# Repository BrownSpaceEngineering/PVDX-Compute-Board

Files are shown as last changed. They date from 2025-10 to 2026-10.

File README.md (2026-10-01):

# PVDX Compute Board

This repo contains kicad files for the PVDX Compute board, the main command/control interface for PVDX. The board contains: the SAMD51 microcontroller, 3 MRAM chips, an accelerometer, a 3-axis magnetometer, and headers for interfacing with the EPS, the battery board, the burn wire, the photodiodes, the ADCS/perovskite boards, the S-Band, the UHF, the display, and the ArduCam. 

The repo is organized into four main folders: 
1. Components (kicad symbols, footprints, and step files for each component not already built into the kicad libraries; shared between the other three folders)
2. SAMD51 Devboard (a simplified version for testing; it is run off USB-C, and houses only buck converters (not present on the final boards) and the SAMD51. All other components are exposed as headers. Every pin on the SAMD51 is also exposed)
3. Compute Board (the two layer implementation of the unified board containing all the final flight components with headers only for peripherals)
4. compute4layer (a copy of the Compute Board project with only the layout changed to a 4-layer (signal, GND, power, signal) stackup)

## Schematics 

Presented here are images of the schematics shared by the Compute Board and compute4layer: 




## Datasheets

For ease of access, here is a table of datasheets for the onboard components: 

| Component | Part number |
| --- | --- |
| SAMD51 | [Microchip ATSAMD51N19A](https://ww1.microchip.com/downloads/aemDocuments/documents/MCU32/ProductDocuments/DataSheets/SAM-D5x-E5x-Family-Data-Sheet-DS60001507.pdf) |
| MRAM | [Everspin EM008LX](https://datasheet.lcsc.com/datasheet/pdf/902c3bb2baf214246dee551af985b64a.pdf?productCode=C17289052) |
| Accelerometer | [Murata SCH16T-K01](https://sensorsandpower.angst-pfister.com/fileadmin/images/news/Datasheet-SCH16T-K01_JAN2024.pdf) |
| Magnetometer | [PNI RM3100](https://www.tri-m.com/products/pni/RM3100-User-Manual.pdf) |
| Buck converter | [Microchip MCP-1604-180I](https://ww1.microchip.com/downloads/aemDocuments/documents/OTH/ProductDocuments/DataSheets/22042B.pdf) |
| I2C Multiplexer | [TI TCA9546A](https://www.ti.com/lit/ds/symlink/tca9546a.pdf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) |

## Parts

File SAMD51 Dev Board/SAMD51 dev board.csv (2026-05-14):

Reference | Qty | Value | DNP | Exclude from BOM | Exclude from Board | Footprint | Datasheet | Manufacturer_Part_Number | Manufacturer_Name
C1,C2,C3,C4,C7,COUT1 | 6 | 4.7 uF |  |  |  | Capacitor_SMD:C_0402_1005Metric
C5,CIN1,CIN2,CIN3 | 4 | 10 uF |  |  |  | Capacitor_SMD:C_0402_1005Metric
C6 | 1 | 0.1 uF |  |  |  | Capacitor_SMD:C_0402_1005Metric
CIN4,CIN5,CIN6,COUT2 | 4 | 100 nF |  |  |  | Capacitor_SMD:C_0402_1005Metric
D1 | 1 | RED |  |  |  | LED_SMD:LED_0402_1005Metric
D2 | 1 | GREEN |  |  |  | LED_SMD:LED_0402_1005Metric
D3,D4 | 2 | ORANGE |  |  |  | LED_SMD:LED_0402_1005Metric
IC1 | 1 | MCP1603-330I_MC |  |  |  | MPC1603:MPC1603-330 | https://static6.arrow.com/aropdfconversion/4acbe9a1e3d4dc5e34c6ab3aecc61a4631ca5442/22042a.pdf | MCP1603-330I/MC | Microchip
IC2 | 1 | MCP1603-180I_MC |  |  |  | MPC1603:MPC1603-180 | https://static6.arrow.com/aropdfconversion/4acbe9a1e3d4dc5e34c6ab3aecc61a4631ca5442/22042a.pdf | MCP1603-330I/MC | Microchip
J1 | 1 | Conn_02x08_Top_Bottom |  |  |  | Connector_PinSocket_2.54mm:PinSocket_2x08_P2.54mm_Vertical
J2 | 1 | USB4105-GF-A |  |  |  | USBC:USB4105_GCT | USB4105-GF-A
J3 | 1 | FTSH-105-01-L-DV-007-K |  |  |  | JLink:SAMTEC_FTSH-105-01-L-DV-007-K
J4,J11 | 2 | Conn_01x07 |  |  |  | Connector_PinSocket_2.54mm:PinSocket_1x07_P2.54mm_Vertical
J5,J10,J14 | 3 | Conn_02x16_Top_Bottom |  |  |  | Connector_PinSocket_2.54mm:PinSocket_2x16_P2.54mm_Vertical
J6 | 1 | Conn_02x06_Top_Bottom |  |  |  | Connector_PinSocket_2.54mm:PinSocket_2x06_P2.54mm_Vertical
J7 | 1 | Conn_02x08_Counter_Clockwise |  |  |  | Connector_PinSocket_2.54mm:PinSocket_2x08_P2.54mm_Vertical
J8,J17 | 2 | Conn_01x10 |  |  |  | Connector_PinSocket_2.54mm:PinSocket_1x10_P2.54mm_Vertical
J9 | 1 | Conn_01x02 |  |  |  | Connector_PinSocket_2.54mm:PinSocket_1x02_P2.54mm_Vertical
J12 | 1 | Conn_01x05 |  |  |  | Connector_PinSocket_2.54mm:PinSocket_1x05_P2.54mm_Vertical
J13 | 1 | Conn_01x08 |  |  |  | Connector_PinSocket_2.54mm:PinSocket_1x08_P2.54mm_Vertical
J15,J16,J19 | 3 | Conn_01x06 |  |  |  | Connector_PinSocket_2.54mm:PinSocket_1x06_P2.54mm_Vertical
L1,L2 | 2 | 4.7uH |  |  |  | Inductor_SMD:L_0201_0603Metric
L3,L4 | 2 | 10 uH |  |  |  | Inductor_SMD:L_0402_1005Metric
R1,R2,R3,R4 | 4 | 1K |  |  |  | Resistor_SMD:R_0402_1005Metric
R5,R8 | 2 | 5.1k |  |  |  | Resistor_SMD:R_01005_0402Metric
R6,R7 | 2 | 22 |  |  |  | Resistor_SMD:R_01005_0402Metric
R9,R10 | 2 | 0 |  |  |  | Resistor_SMD:R_0402_1005Metric
R11,R12,R13,R14 | 4 | 10k |  |  |  | Resistor_SMD:R_0402_1005Metric
U1 | 1 | SAMD51 |  |  |  | SAMD51:TQFP128_14X14MC_MCH-L

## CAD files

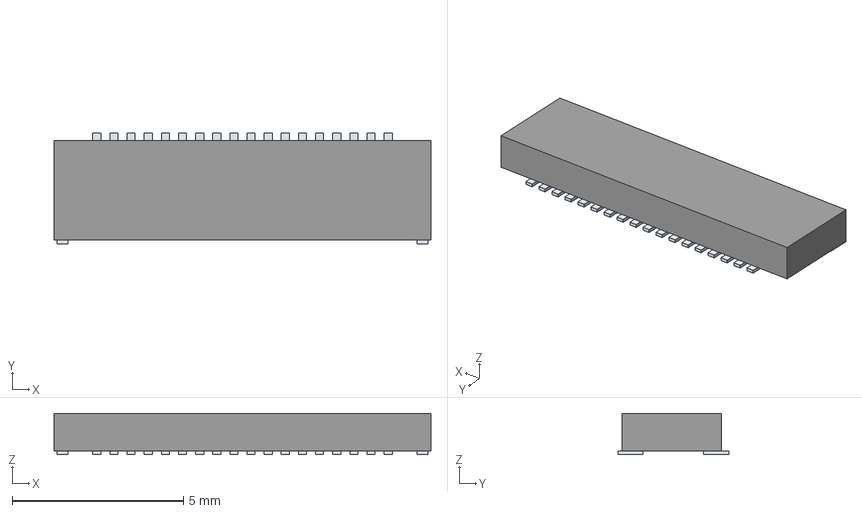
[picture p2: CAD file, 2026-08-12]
Components/18 Pin Ribbon Cable/FH34SRJ-18S-0.5SH_50_.stp
11.0 x 3.23 x 1.20 mm
Pins

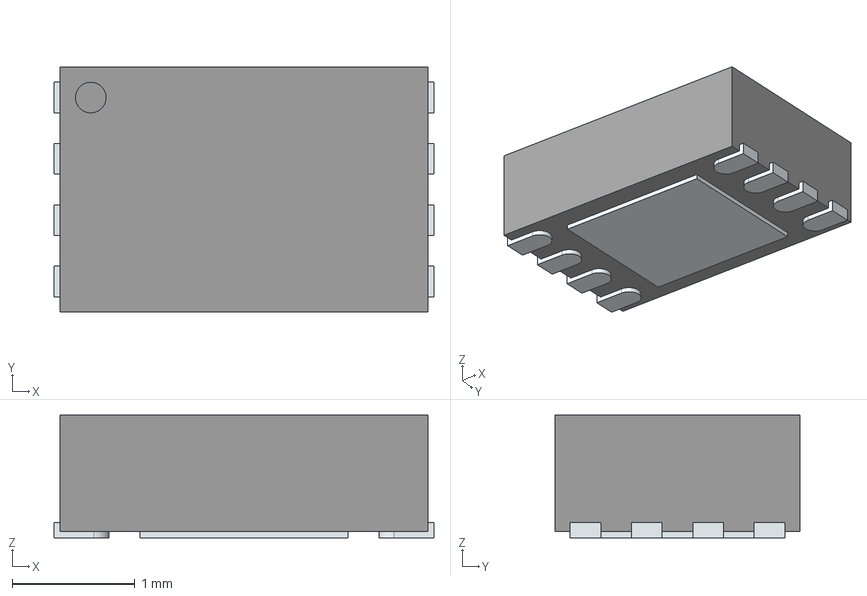
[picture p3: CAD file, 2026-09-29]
Components/Buck converters/MCP1603-330I_MC.stp
3.10 x 2.00 x 1.00 mm
ThermalPin
PinsArrayLR

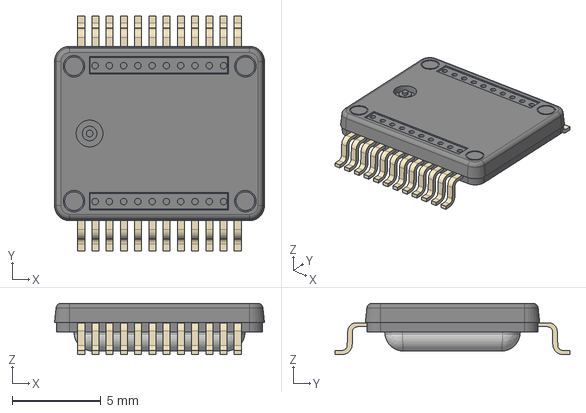
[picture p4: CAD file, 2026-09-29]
Components/Gyroscope/SCH16T-K01-1.stp
11.8 x 13.2 x 2.87 mm

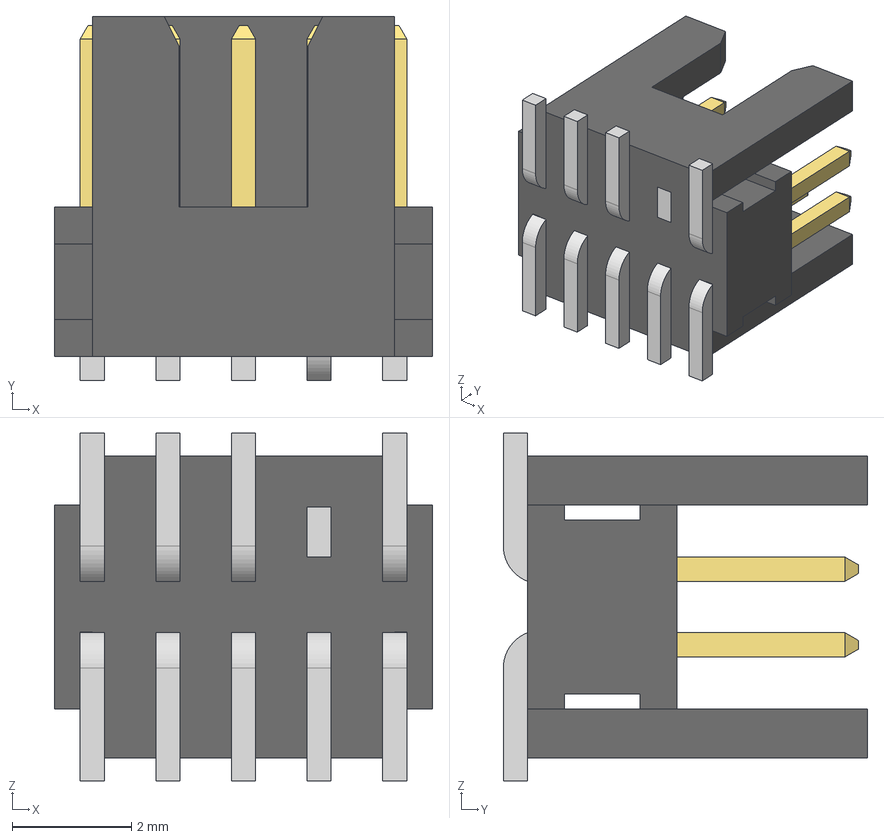
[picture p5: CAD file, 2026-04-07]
Components/J Link/FTSH-105-01-L-DV-007-K.step
6.35 x 6.12 x 5.84 mm
FTSH-105-01-L-DV-007-K_body
FTSH-105-01-L-DV-007-K_pins1
FTSH-105-01-L-DV-007-K_pins2

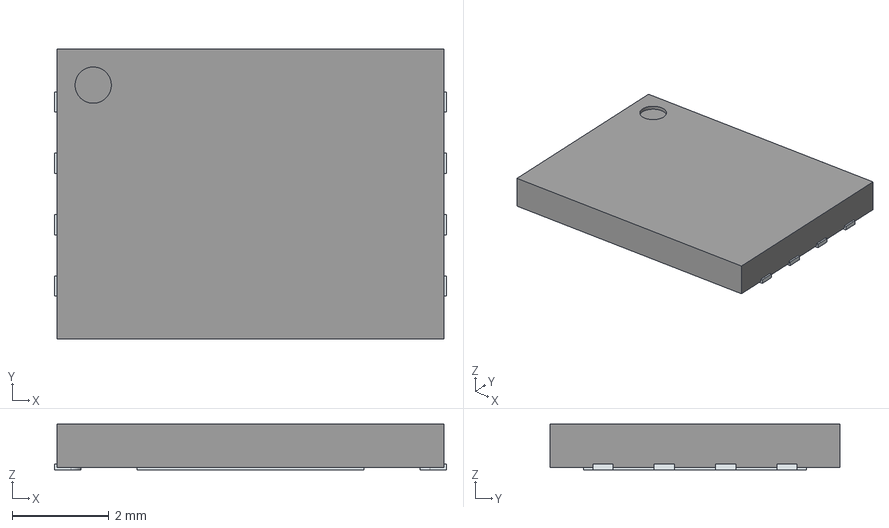
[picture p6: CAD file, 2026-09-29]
Components/MRAM/EM008LXQADG13IS1T.stp
8.10 x 6.00 x 0.95 mm
ThermalPin
PinsArrayLR

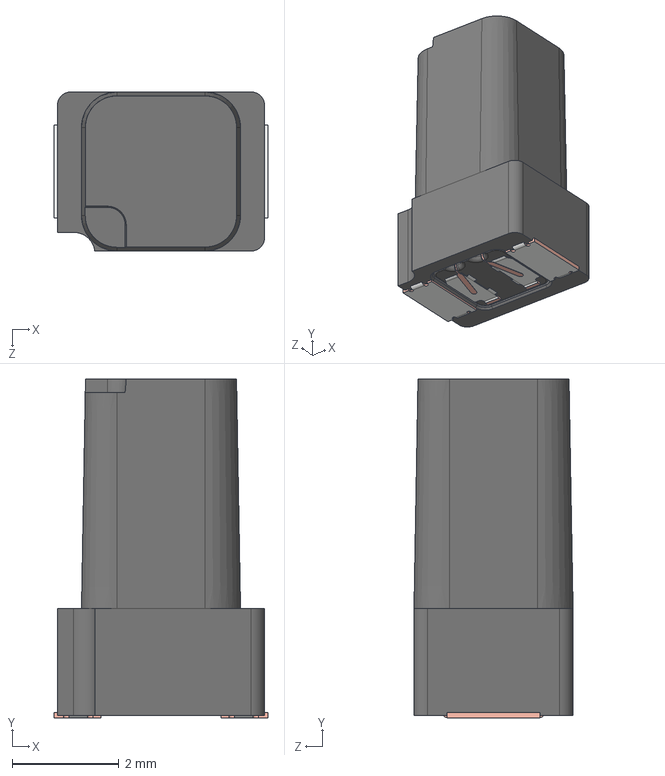
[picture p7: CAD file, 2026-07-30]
Components/RM3100/Sensor Sen-Z-f.STEP
4.00 x 6.35 x 2.98 mm

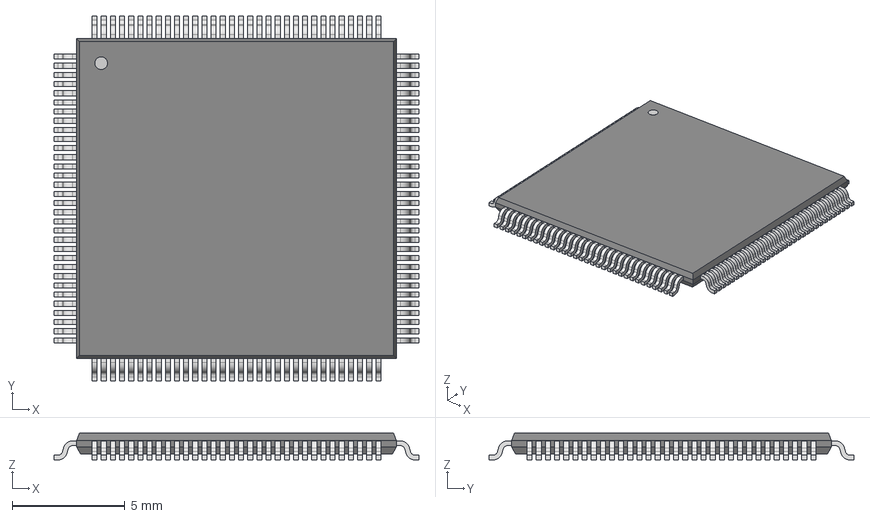
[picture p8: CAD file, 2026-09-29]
Components/SAMD51/TQFP128_14X14MC_MCH.step
16.2 x 16.2 x 1.20 mm

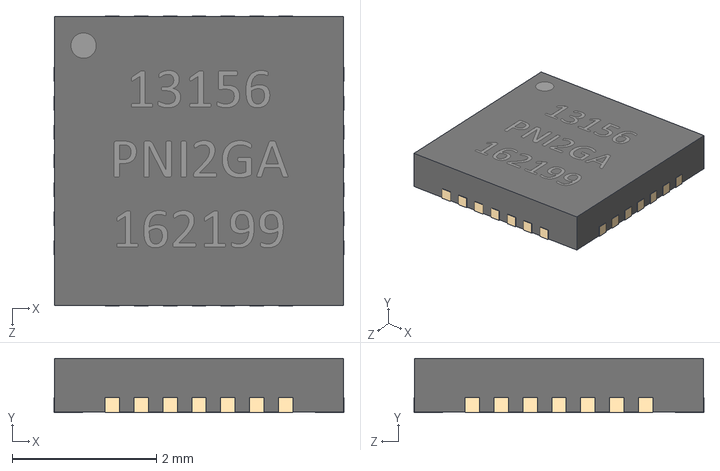
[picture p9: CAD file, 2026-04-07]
SAMD51 Dev Board/Components/RM3100/MagIC QFN 4X4.STEP
4.02 x 0.75 x 4.02 mm

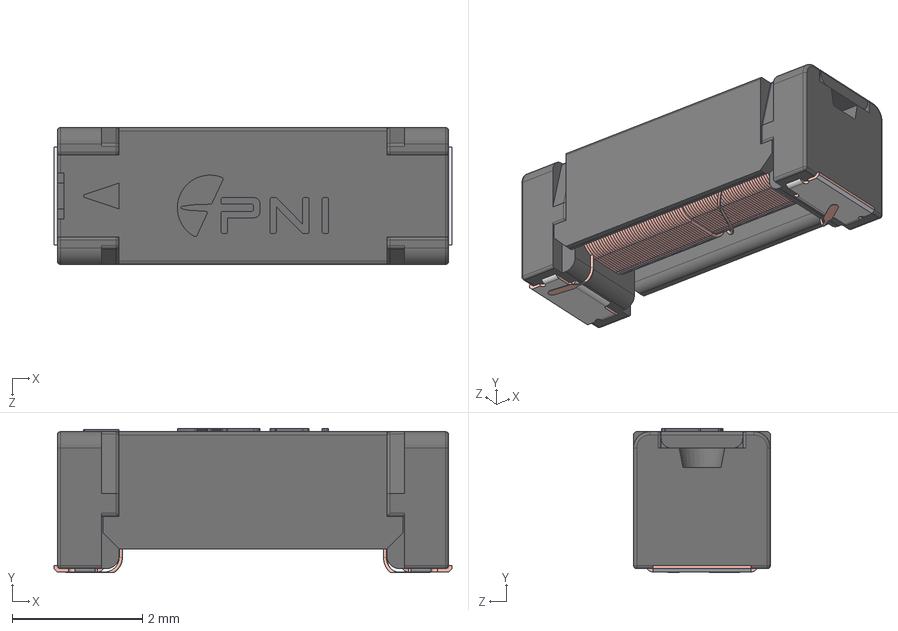
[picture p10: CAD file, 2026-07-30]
Components/RM3100/Sensor, Sen-XY-f.STEP
6.10 x 2.21 x 2.10 mm

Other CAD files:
Components/18 Pin Ribbon Cable/chips.prt
Components/18 Pin Ribbon Cable/fh34srj18s05sh50.psm

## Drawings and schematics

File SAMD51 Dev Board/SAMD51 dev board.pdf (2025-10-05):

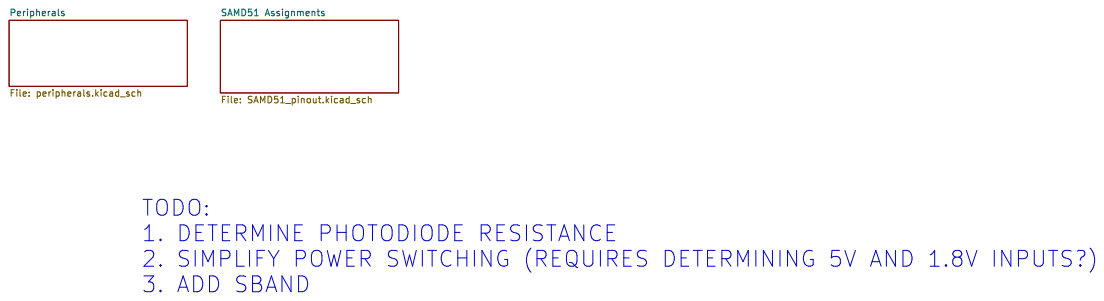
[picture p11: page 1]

1 TODO:
1. DETERMINE PHOTODIODE RESISTANCE
2. SIMPLIFY POWER SWITCHING (REQUIRES DETERMINING 5V AND 1.8V INPUTS?)
3. ADD SBAND

Milan Capoor PVDX COMPUTE BOARD

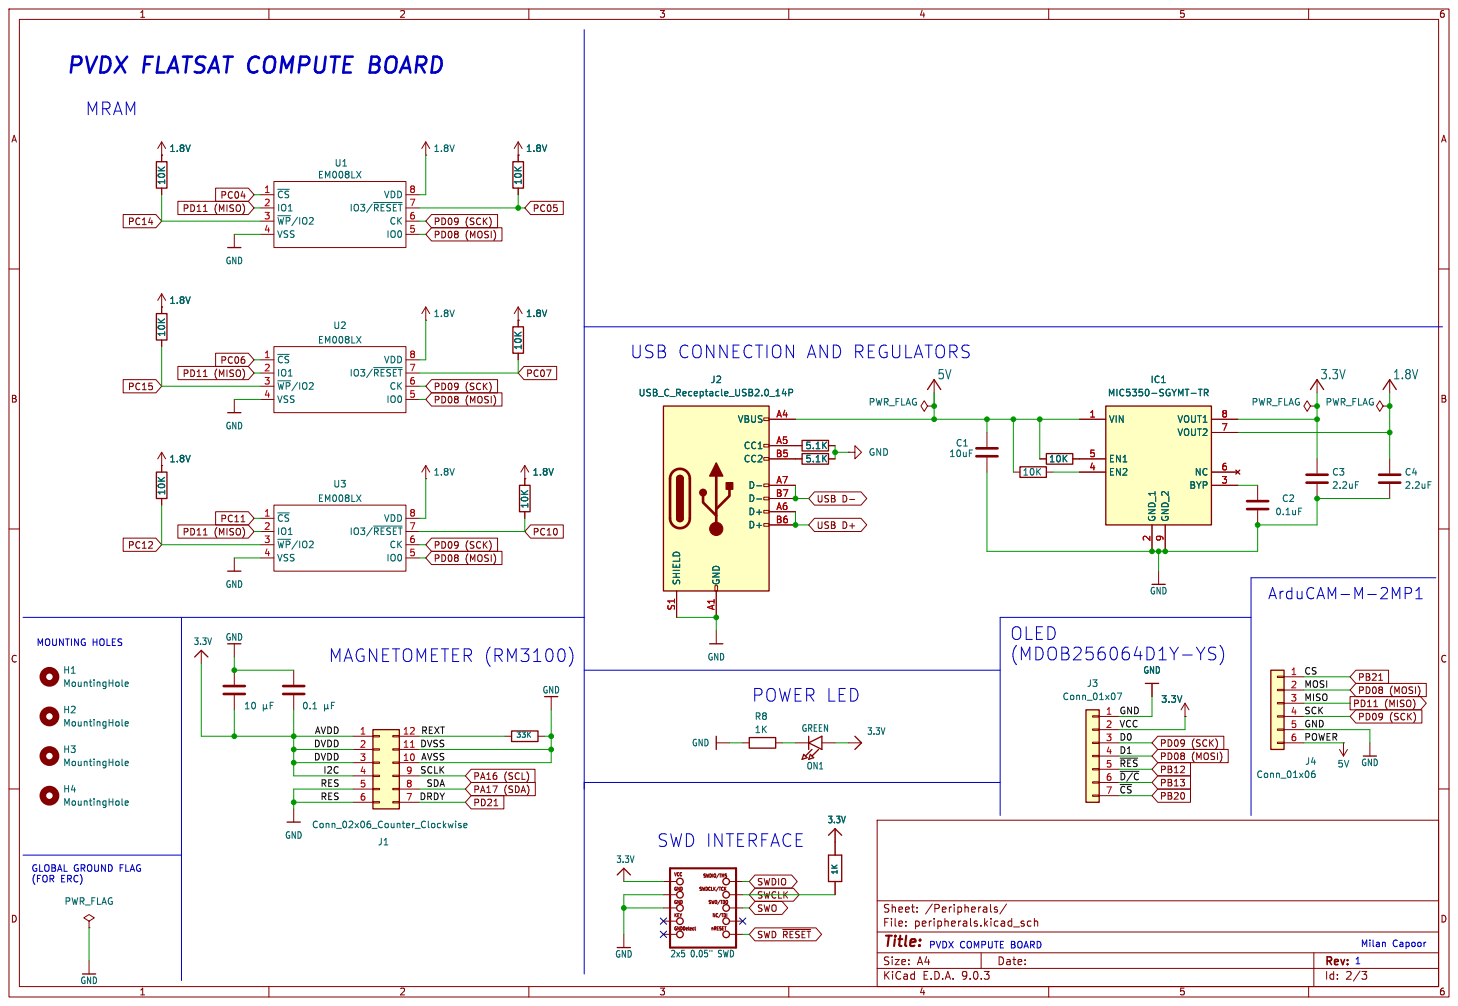
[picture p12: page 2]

PVDX FLATSAT COMPUTE BOARD

USB CONNECTION AND REGULATORS

(MDOB256064D1Y-YS) GLOBAL GROUND FLAG

MAGNETOMETER (RM3100)
CS REXT RES DVDD

KEY GNDDetect SWDCLK/TCK

Id: 2/3 Title: File: peripherals.kicad_sch Sheet: /Peripherals/

nRESET NC/TDI 2x5 0.05" SWD

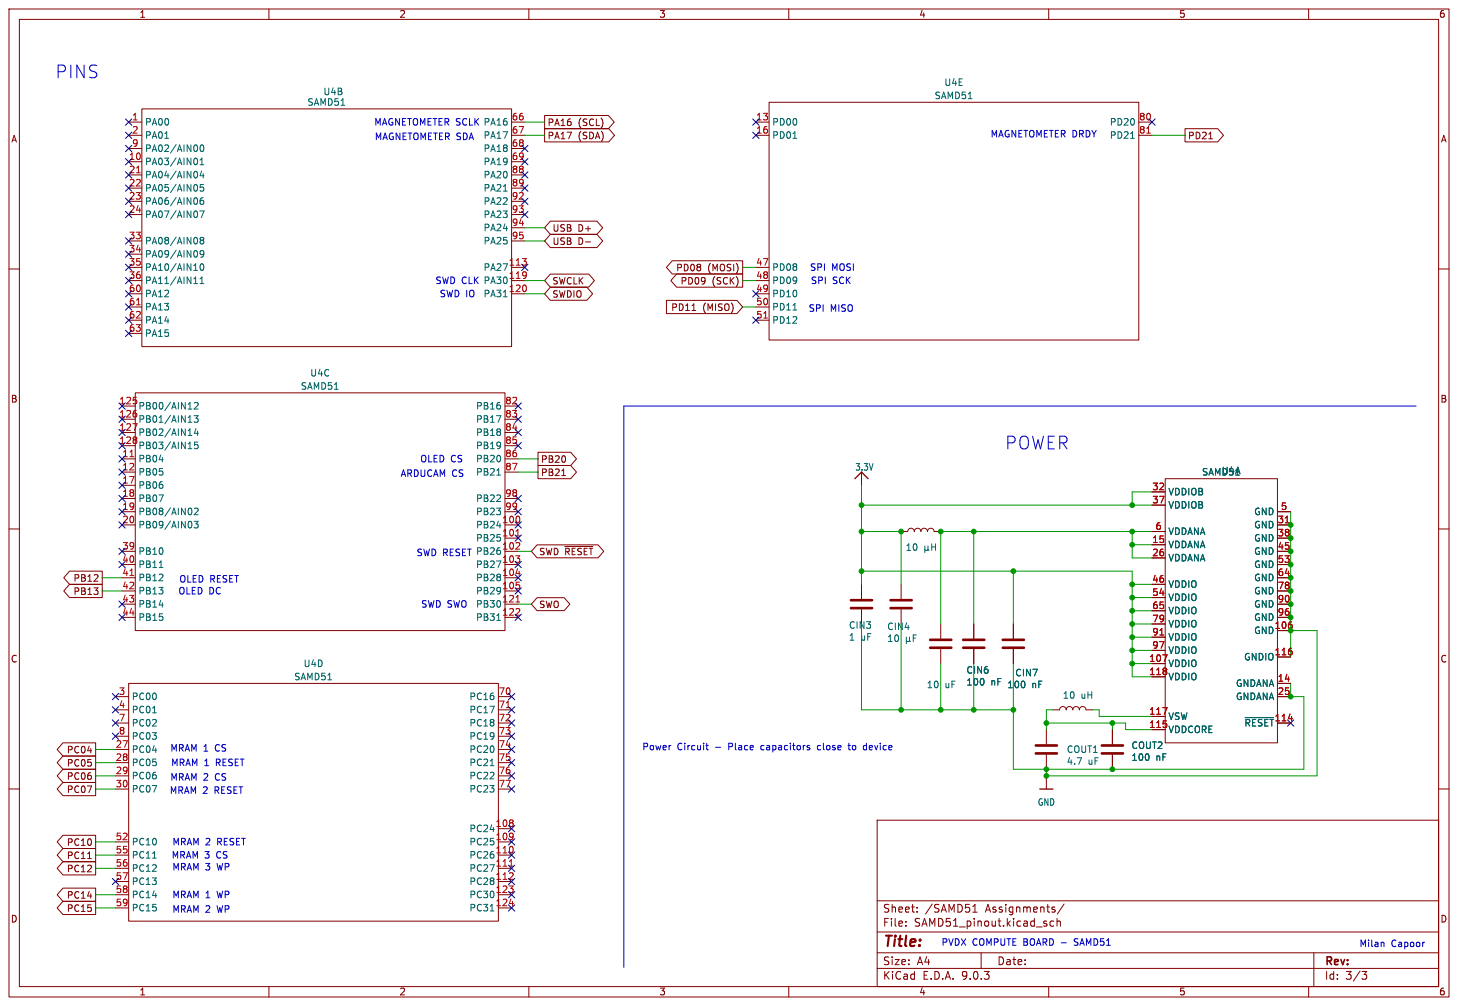
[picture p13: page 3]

OLED CS MAGNETOMETER SDA MAGNETOMETER SCLK

USB D- USB D+ MRAM 2 RESET MRAM 1 WP MRAM 2 CS MRAM 2 WP MRAM 3 WP MRAM 3 CS MRAM 1 RESET MRAM 2 RESET OLED RESET MRAM 1 CS

SPI MOSI SPI SCK

SWD CLK
SWD RESET SWD IO

ARDUCAM CS OLED DC

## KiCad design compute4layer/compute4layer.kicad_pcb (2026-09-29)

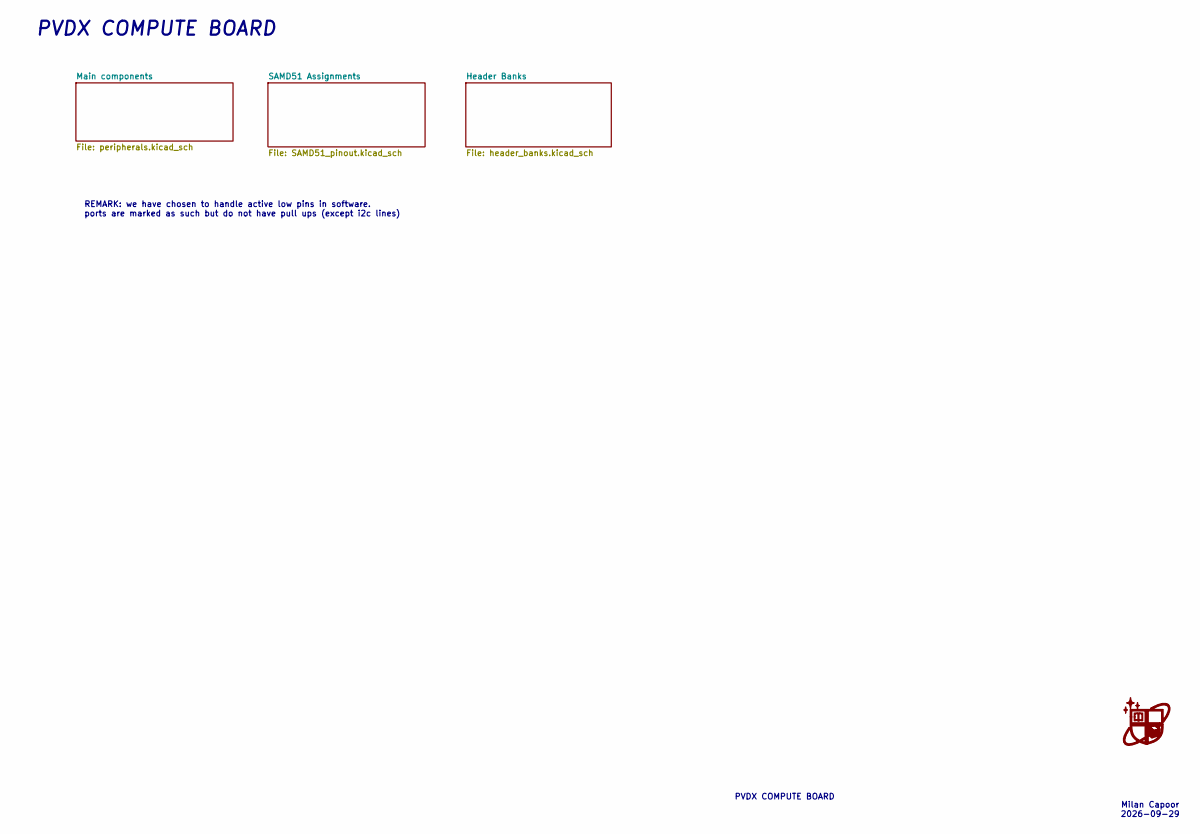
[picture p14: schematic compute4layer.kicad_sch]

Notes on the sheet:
REMARK: we have chosen to handle active low pins in software. ports are marked as such but do not have pull ups (except i2c lines)
Milan Capoor 2026-09-29
PVDX COMPUTE BOARD
PVDX COMPUTE BOARD

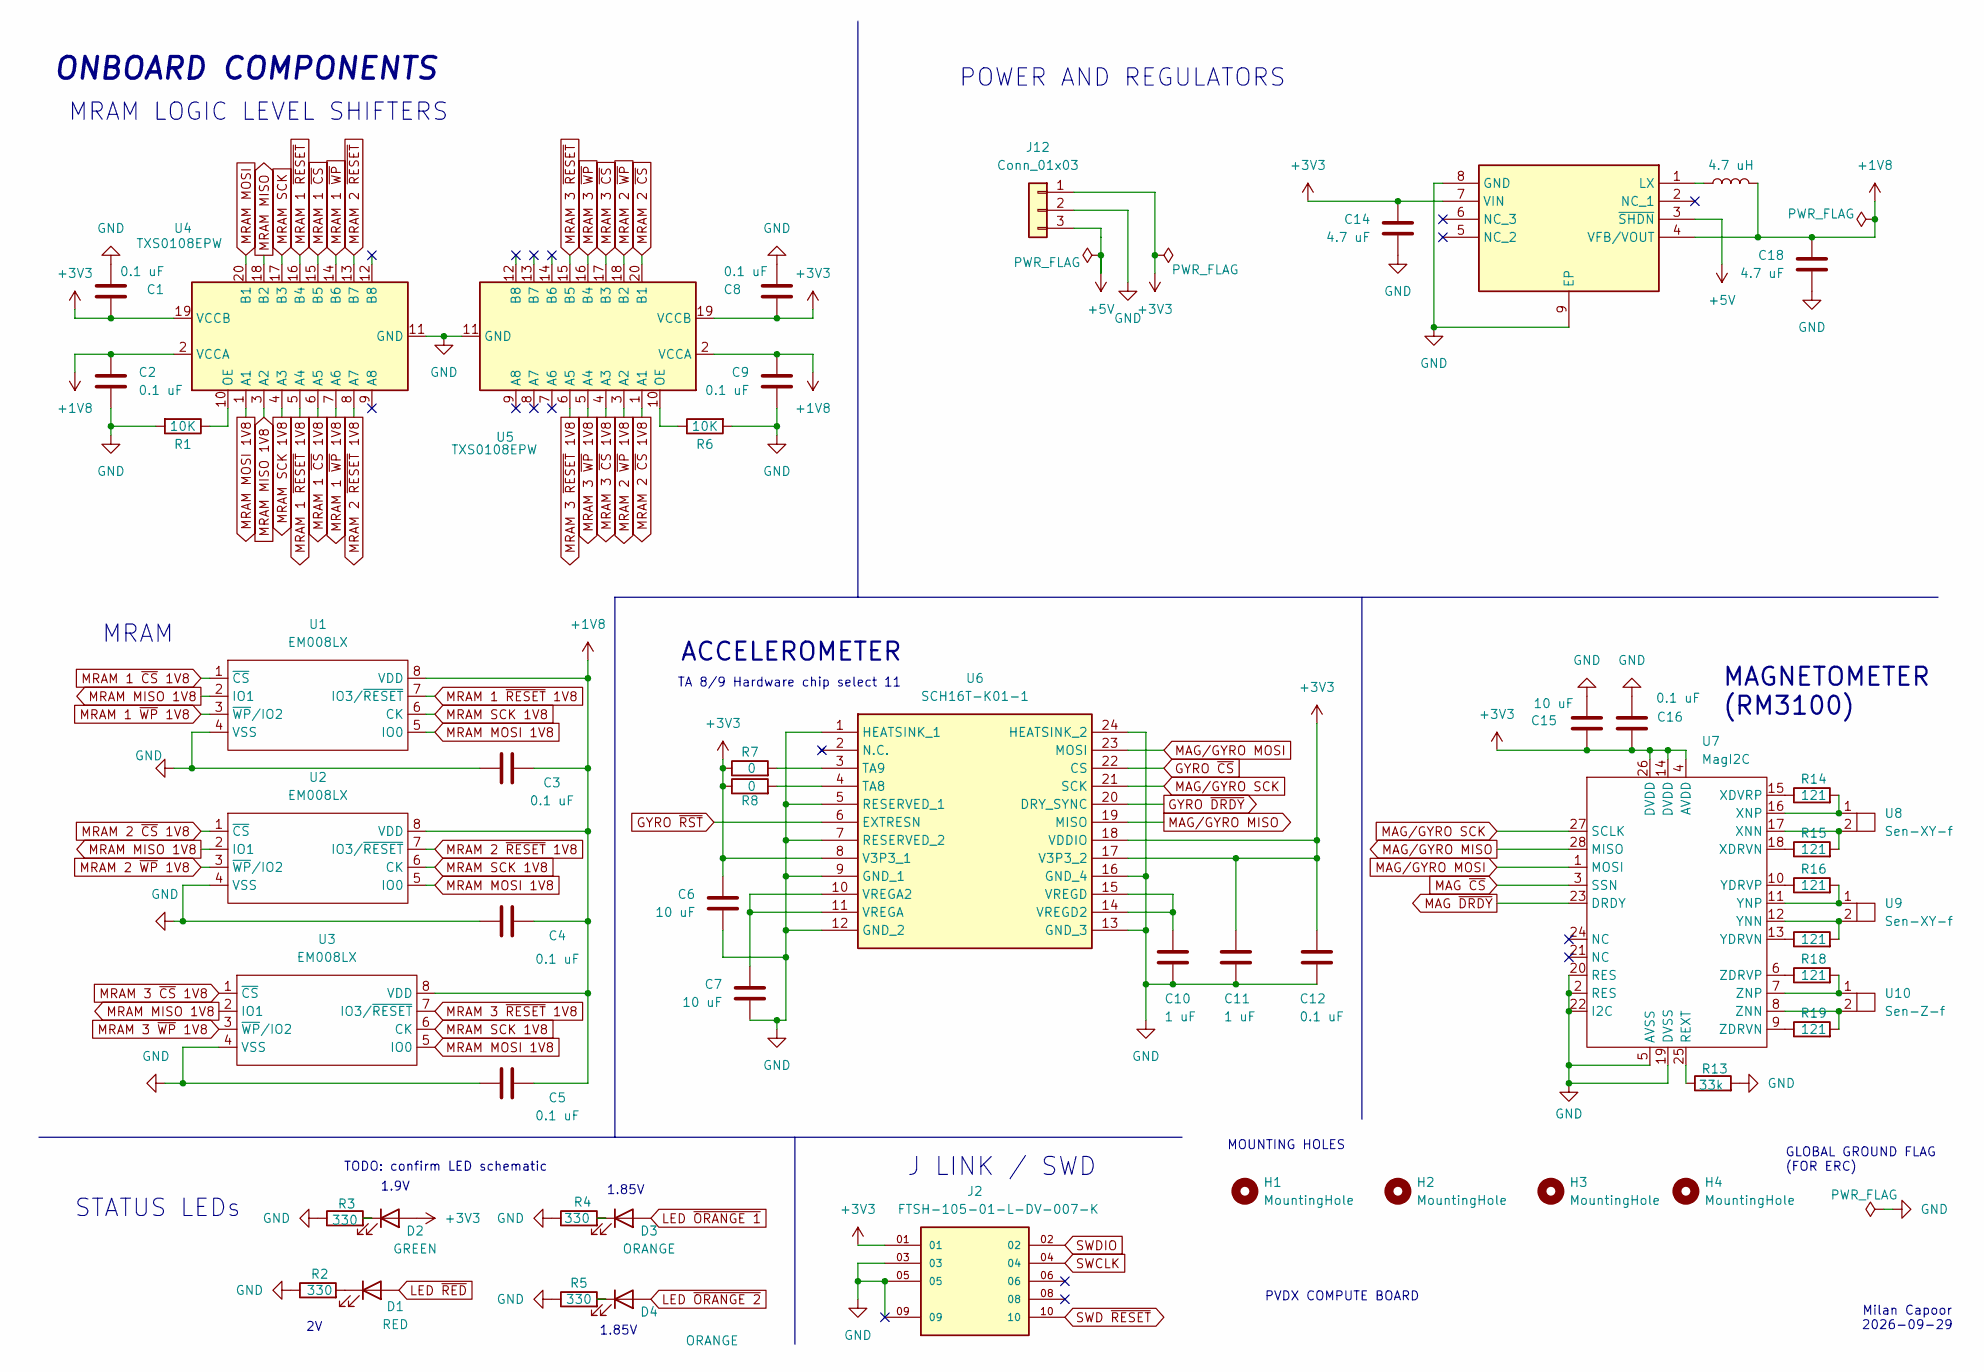
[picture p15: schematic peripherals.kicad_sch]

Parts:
C1, C2, C3, C4, C5, C8, C9, C12, C16: 0.1 uF; C_0603_1608Metric
C6, C7, C15: 10 uF; C_0603_1608Metric
C10, C11: 1 uF; C_0603_1608Metric
C14, C18: 4.7 uF; C_0603_1608Metric
D1: RED; LED_0603_1608Metric
D2: GREEN; LED_0603_1608Metric
D3, D4: ORANGE; LED_0603_1608Metric
H1, H2, H3, H4: MountingHole; MountingHole_3.2mm_M3
IC2: MCP1603-180I_MC; MPC1603-180; Mouser Part Number 579-MCP1603-330I/MC
J2: FTSH-105-01-L-DV-007-K; SAMTEC_FTSH-105-01-L-DV-007-K; PARTREV H
J12: Conn_01x03; PinSocket_1x03_P2.54mm_Vertical
L2: 4.7 uH; L_0603_1608Metric
R1, R6: 10K; R_0603_1608Metric
R2, R3, R4, R5: 330; R_0603_1608Metric
R7, R8: 0; R_0603_1608Metric
R13: 33k; R_0603_1608Metric
R14, R15, R16, R17, R18, R19: 121; R_0603_1608Metric
U1, U2, U3: EM008LX; EM008LXQADG13IS1T
U4, U5: TXS0108EPW; TSSOP-20_4.4x6.5mm_P0.65mm
U6: SCH16T-K01-1; SCH16TK011; Mouser Part Number 81-SCH16T-K01-1
U7: MagI2C
U8, U9: Sen-XY-f
U10: Sen-Z-f

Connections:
+1V8: C2.1, C3.2, C4.2, C5.2, C9.1, C18.1, IC2.4 (VFB/VOUT), L2.2, U1.8 (VDD), U2.8 (VDD), U3.8 (VDD), U4.2 (VCCA), U5.2 (VCCA)
+3V3: C1.1, C6.1, C8.1, C11.1, C12.1, C14.1, C15.2, C16.2, D2.2 (A), IC2.7 (VIN), J2.01, J12.1, R7.1, R8.1, U4.19 (VCCB), U5.19 (VCCB), U6.8 (V3P3_1), U6.17 (V3P3_2), U6.18 (VDDIO), U7.4 (AVDD), U7.14 (DVDD), U7.26 (DVDD); also elsewhere on the board
+5V: IC2.3 (~SHDN), J12.3; also elsewhere on the board
GND: C1.2, C2.2, C3.1, C4.1, C5.1, C6.2, C7.2, C8.2, C9.2, C10.2, C11.2, C12.2, C14.2, C15.1, C16.1, C18.2, IC2.8 (GND), IC2.9 (EP), J2.03, J2.05, J2.09, J12.2, R1.2, R2.1, R3.1, R4.1, R5.1, R6.2, R13.2, U1.4 (VSS), U2.4 (VSS), U3.4 (VSS), U4.11 (GND), U5.11 (GND), U6.1 (HEATSINK_1), U6.5 (RESERVED_1), U6.7 (RESERVED_2), U6.9 (GND_1), U6.12 (GND_2), U6.13 (GND_3), U6.16 (GND_4), U6.24 (HEATSINK_2), U7.2 (RES), U7.5 (AVSS), U7.19 (DVSS), U7.20 (RES), U7.22 (I2C); also elsewhere on the board
GYRO ~CS: U6.22 (CS); also elsewhere on the board
GYRO ~DRDY: U6.20 (DRY_SYNC); also elsewhere on the board
GYRO ~RST: U6.6 (EXTRESN); also elsewhere on the board
LED ~ORANGE 1: D3.2 (A); also elsewhere on the board
LED ~ORANGE 2: D4.2 (A); also elsewhere on the board
LED ~RED: D1.2 (A); also elsewhere on the board
MAG ~CS: U7.3 (SSN); also elsewhere on the board
MAG ~DRDY: U7.23 (DRDY); also elsewhere on the board
MAG/GYRO MISO: U6.19 (MISO), U7.28 (MISO); also elsewhere on the board
MAG/GYRO MOSI: U6.23 (MOSI), U7.1 (MOSI); also elsewhere on the board
MAG/GYRO SCK: U6.21 (SCK), U7.27 (SCLK); also elsewhere on the board
MRAM 1 ~CS: U4.15 (B5); also elsewhere on the board
MRAM 1 ~CS 1V8: U1.1 (~CS), U4.6 (A5)
MRAM 1 ~RESET: U4.16 (B4); also elsewhere on the board
MRAM 1 ~RESET 1V8: U1.7 (IO3/~RESET), U4.5 (A4)
MRAM 1 ~WP: U4.14 (B6); also elsewhere on the board
MRAM 1 ~WP 1V8: U1.3 (~WP/IO2), U4.7 (A6)
MRAM 2 ~CS: U5.20 (B1); also elsewhere on the board
MRAM 2 ~CS 1V8: U2.1 (~CS), U5.1 (A1)
MRAM 2 ~RESET: U4.13 (B7); also elsewhere on the board
MRAM 2 ~RESET 1V8: U2.7 (IO3/~RESET), U4.8 (A7)
MRAM 2 ~WP: U5.18 (B2); also elsewhere on the board
MRAM 2 ~WP 1V8: U2.3 (~WP/IO2), U5.3 (A2)
MRAM 3 ~CS: U5.17 (B3); also elsewhere on the board
MRAM 3 ~CS 1V8: U3.1 (~CS), U5.4 (A3)
MRAM 3 ~RESET: U5.15 (B5); also elsewhere on the board
MRAM 3 ~RESET 1V8: U3.7 (IO3/~RESET), U5.6 (A5)
MRAM 3 ~WP: U5.16 (B4); also elsewhere on the board
MRAM 3 ~WP 1V8: U3.3 (~WP/IO2), U5.5 (A4)
MRAM MISO: U4.18 (B2); also elsewhere on the board
MRAM MISO 1V8: U1.2 (IO1), U2.2 (IO1), U3.2 (IO1), U4.3 (A2)
MRAM MOSI: U4.20 (B1); also elsewhere on the board
MRAM MOSI 1V8: U1.5 (IO0), U2.5 (IO0), U3.5 (IO0), U4.1 (A1)
MRAM SCK: U4.17 (B3); also elsewhere on the board
MRAM SCK 1V8: U1.6 (CK), U2.6 (CK), U3.6 (CK), U4.4 (A3)
unnamed: D1.1 (K), R2.2
unnamed: D2.1 (K), R3.2
unnamed: D3.1 (K), R4.2
unnamed: D4.1 (K), R5.2
unnamed: IC2.1 (LX), L2.1
unnamed: R1.1, U4.10 (OE)
unnamed: R6.1, U5.10 (OE)
unnamed: R8.2, U6.4 (TA8)
unnamed: R7.2, U6.3 (TA9)
unnamed: C7.1, U6.10 (VREGA2), U6.11 (VREGA)
unnamed: C10.1, U6.14 (VREGD2), U6.15 (VREGD)
unnamed: R13.1, U7.25 (REXT)
unnamed: R15.1, U7.18 (XDRVN)
unnamed: R14.1, U7.15 (XDVRP)
unnamed: R15.2, U7.17 (XNN), U8.2
unnamed: R14.2, U7.16 (XNP), U8.1
unnamed: R17.1, U7.13 (YDRVN)
unnamed: R16.1, U7.10 (YDRVP)
unnamed: R17.2, U7.12 (YNN), U9.2
unnamed: R16.2, U7.11 (YNP), U9.1
unnamed: R19.1, U7.9 (ZDRVN)
unnamed: R18.1, U7.6 (ZDRVP)
unnamed: R19.2, U7.8 (ZNN), U10.2
unnamed: R18.2, U7.7 (ZNP), U10.1
SWCLK: J2.04; also elsewhere on the board
SWD ~RESET: J2.10; also elsewhere on the board
SWDIO: J2.02; also elsewhere on the board

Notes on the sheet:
POWER AND REGULATORS
MAGNETOMETER (RM3100)
STATUS LEDs
ACCELEROMETER
ONBOARD COMPONENTS
GLOBAL GROUND FLAG (FOR ERC)
1.85V
MRAM LOGIC LEVEL SHIFTERS
J LINK / SWD
MOUNTING HOLES
PVDX COMPUTE BOARD
1.9V
TA 8/9 Hardware chip select 11
TODO: confirm LED schematic
Milan Capoor 2026-09-29
MRAM

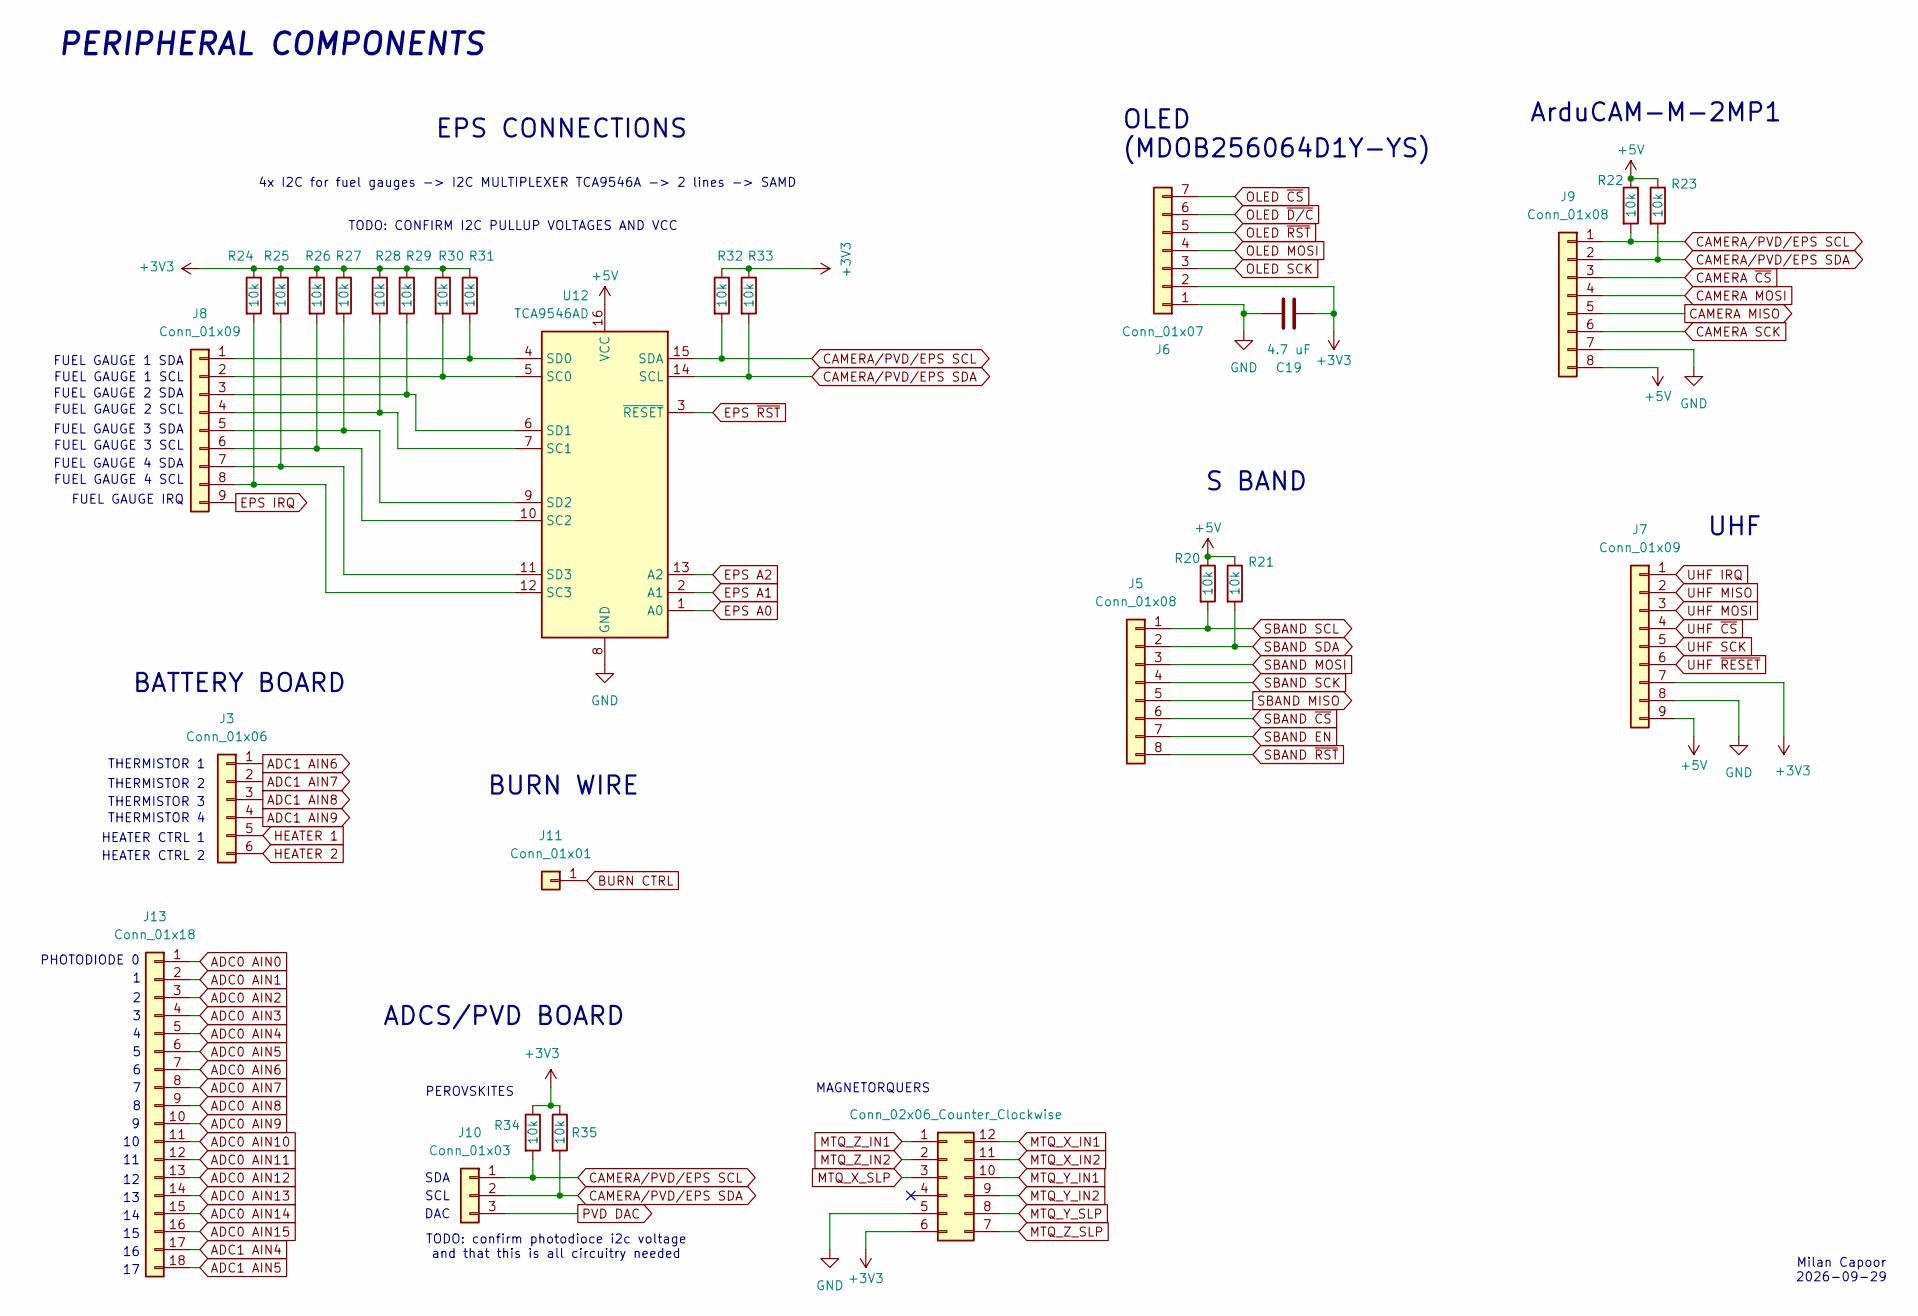
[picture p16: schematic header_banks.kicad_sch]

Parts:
C19: 4.7 uF; C_0603_1608Metric
J3: Conn_01x06; PinSocket_1x06_P2.54mm_Vertical
J4: Conn_02x06_Counter_Clockwise; PinSocket_2x06_P2.54mm_Vertical
J5, J9: Conn_01x08; PinSocket_1x08_P2.54mm_Vertical
J6: Conn_01x07; PinSocket_1x07_P2.54mm_Vertical
J7, J8: Conn_01x09; PinSocket_1x09_P2.54mm_Vertical
J10: Conn_01x03; PinSocket_1x03_P2.54mm_Vertical
J11: Conn_01x01; PinSocket_1x01_P2.54mm_Vertical
J13: Conn_01x18; FH34SRJ18S05SH50
R20, R21, R22, R23, R24, R25, R26, R27, R28, R29, R30, R31, R32, R33, R34, R35: 10k; R_0603_1608Metric
U12: TCA9546AD; SOIC-16_3.9x9.9mm_P1.27mm

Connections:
+3V3: C19.2, J4.6, J6.2, J7.7, R24.1, R25.1, R26.1, R27.1, R28.1, R29.1, R30.1, R31.1, R32.1, R33.1, R34.1, R35.1; also elsewhere on the board
+5V: J7.9, J9.8, R20.1, R21.1, R22.1, R23.1, U12.16 (VCC); also elsewhere on the board
ADC0 AIN0: J13.1; also elsewhere on the board
ADC0 AIN1: J13.2; also elsewhere on the board
ADC0 AIN2: J13.3; also elsewhere on the board
ADC0 AIN3: J13.4; also elsewhere on the board
ADC0 AIN4: J13.5; also elsewhere on the board
ADC0 AIN5: J13.6; also elsewhere on the board
ADC0 AIN6: J13.7; also elsewhere on the board
ADC0 AIN7: J13.8; also elsewhere on the board
ADC0 AIN8: J13.9; also elsewhere on the board
ADC0 AIN9: J13.10; also elsewhere on the board
ADC0 AIN10: J13.11; also elsewhere on the board
ADC0 AIN11: J13.12; also elsewhere on the board
ADC0 AIN12: J13.13; also elsewhere on the board
ADC0 AIN13: J13.14; also elsewhere on the board
ADC0 AIN14: J13.15; also elsewhere on the board
ADC0 AIN15: J13.16; also elsewhere on the board
ADC1 AIN4: J13.17; also elsewhere on the board
ADC1 AIN5: J13.18; also elsewhere on the board
ADC1 AIN6: J3.1; also elsewhere on the board
ADC1 AIN7: J3.2; also elsewhere on the board
ADC1 AIN8: J3.3; also elsewhere on the board
ADC1 AIN9: J3.4; also elsewhere on the board
BURN CTRL: J11.1 (Pin_1_1); also elsewhere on the board
CAMERA MISO: J9.5; also elsewhere on the board
CAMERA MOSI: J9.4; also elsewhere on the board
CAMERA SCK: J9.6; also elsewhere on the board
CAMERA ~CS: J9.3; also elsewhere on the board
CAMERA/PVD/EPS SCL: J9.1, J10.1, R22.2, R32.2, R34.2, U12.15 (SDA); also elsewhere on the board
CAMERA/PVD/EPS SDA: J9.2, J10.2, R23.2, R33.2, R35.2, U12.14 (SCL); also elsewhere on the board
EPS A0: U12.1 (A0); also elsewhere on the board
EPS A1: U12.2 (A1); also elsewhere on the board
EPS A2: U12.13 (A2); also elsewhere on the board
EPS IRQ: J8.9; also elsewhere on the board
EPS ~RST: U12.3 (~RESET); also elsewhere on the board
GND: C19.1, J4.5, J6.1, J7.8, J9.7, U12.8 (GND); also elsewhere on the board
HEATER 1: J3.5; also elsewhere on the board
HEATER 2: J3.6; also elsewhere on the board
MTQ_X_IN1: J4.12; also elsewhere on the board
MTQ_X_IN2: J4.11; also elsewhere on the board
MTQ_X_SLP: J4.3; also elsewhere on the board
MTQ_Y_IN1: J4.10; also elsewhere on the board
MTQ_Y_IN2: J4.9; also elsewhere on the board
MTQ_Y_SLP: J4.8; also elsewhere on the board
MTQ_Z_IN1: J4.1; also elsewhere on the board
MTQ_Z_IN2: J4.2; also elsewhere on the board
MTQ_Z_SLP: J4.7; also elsewhere on the board
unnamed: J8.1, R31.2, U12.4 (SD0)
unnamed: J8.2, R30.2, U12.5 (SC0)
unnamed: J8.3, R29.2, U12.6 (SD1)
unnamed: J8.4, R28.2, U12.7 (SC1)
unnamed: J8.5, R27.2, U12.9 (SD2)
unnamed: J8.6, R26.2, U12.10 (SC2)
unnamed: J8.7, R25.2, U12.11 (SD3)
unnamed: J8.8, R24.2, U12.12 (SC3)
OLED MOSI: J6.4; also elsewhere on the board
OLED SCK: J6.3; also elsewhere on the board
OLED ~CS: J6.7; also elsewhere on the board
OLED ~D/C: J6.6; also elsewhere on the board
OLED ~RST: J6.5; also elsewhere on the board
PVD DAC: J10.3; also elsewhere on the board
SBAND EN: J5.7; also elsewhere on the board
SBAND MISO: J5.5; also elsewhere on the board
SBAND MOSI: J5.3; also elsewhere on the board
SBAND SCK: J5.4; also elsewhere on the board
SBAND SCL: J5.1, R20.2; also elsewhere on the board
SBAND SDA: J5.2, R21.2; also elsewhere on the board
SBAND ~CS: J5.6; also elsewhere on the board
SBAND ~RST: J5.8; also elsewhere on the board
UHF IRQ: J7.1; also elsewhere on the board
UHF MISO: J7.2; also elsewhere on the board
UHF MOSI: J7.3; also elsewhere on the board
UHF SCK: J7.5; also elsewhere on the board
UHF ~CS: J7.4; also elsewhere on the board
UHF ~RESET: J7.6; also elsewhere on the board

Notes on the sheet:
MAGNETORQUERS
TODO: confirm photodioce i2c voltage and that this is all circuitry needed
BURN WIRE
FUEL GAUGE 2 SCL
THERMISTOR 3
PERIPHERAL COMPONENTS
OLED (MDOB256064D1Y-YS)
THERMISTOR 4
PHOTODIODE 0
EPS CONNECTIONS
HEATER CTRL 1
SDA
FUEL GAUGE 3 SDA
FUEL GAUGE 1 SDA
4x I2C for fuel gauges -> I2C MULTIPLEXER TCA9546A -> 2 lines -> SAMD
ADCS/PVD BOARD
FUEL GAUGE IRQ
THERMISTOR 2
ArduCAM-M-2MP1
DAC
HEATER CTRL 2
BATTERY BOARD
FUEL GAUGE 1 SCL
UHF
TODO: CONFIRM I2C PULLUP VOLTAGES AND VCC
Milan Capoor 2026-09-29
FUEL GAUGE 4 SCL
THERMISTOR 1
FUEL GAUGE 3 SCL
SCL
PEROVSKITES
S BAND
FUEL GAUGE 4 SDA
FUEL GAUGE 2 SDA

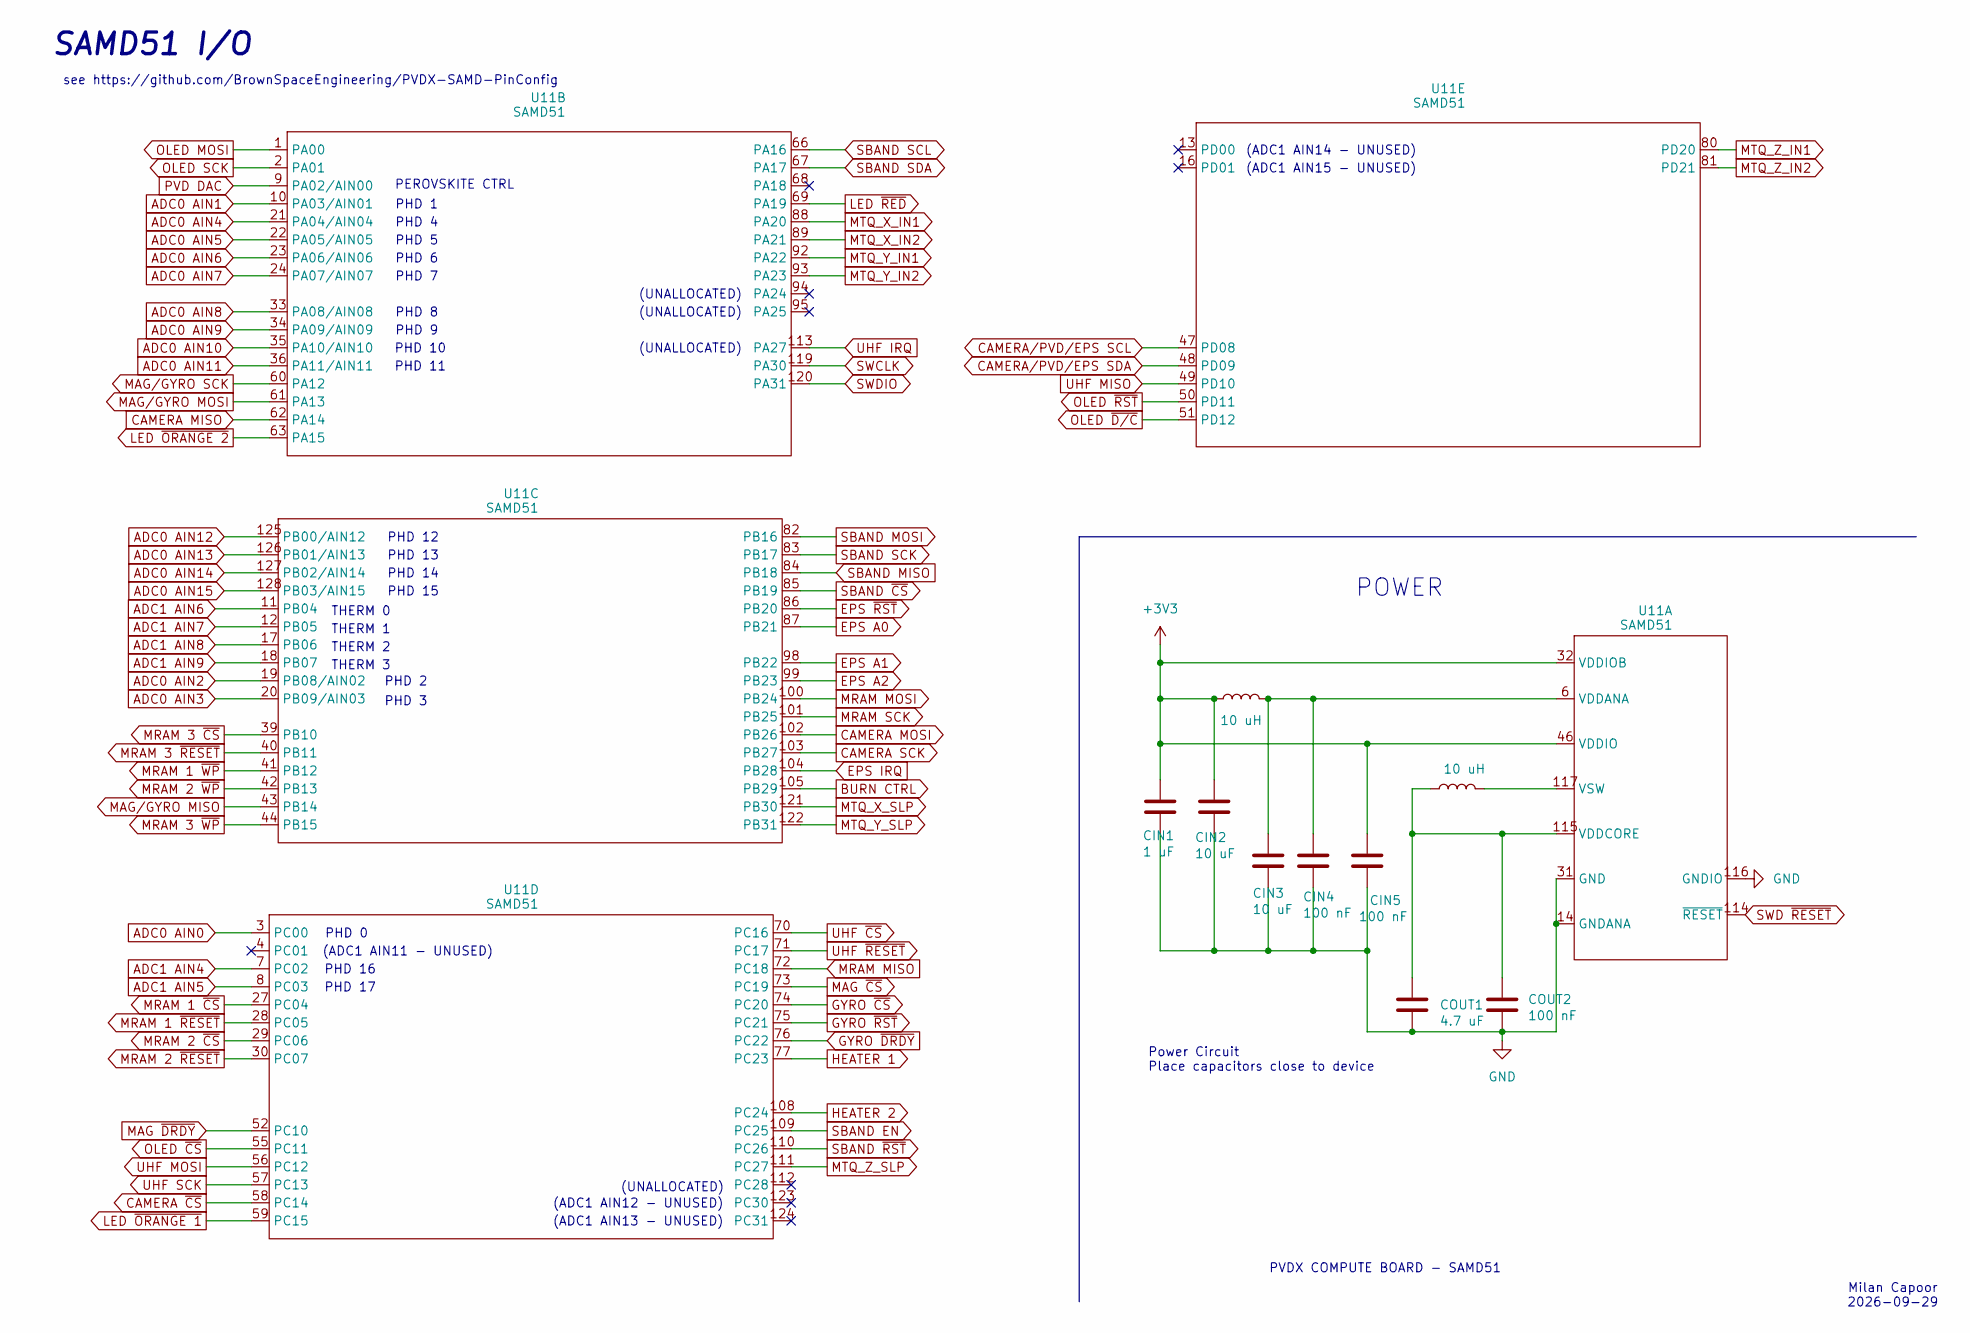
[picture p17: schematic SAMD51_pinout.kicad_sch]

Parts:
CIN1: 1 uF; C_0603_1608Metric
CIN2, CIN3: 10 uF; C_0603_1608Metric
CIN4, CIN5: 100 nF; C_0603_1608Metric
COUT1: 4.7 uF; C_0603_1608Metric
COUT2: 100 nF; C_0603_1608Metric
L3, L4: 10 uH; L_0603_1608Metric
U11: SAMD51; TQFP128_14X14MC_MCH-L

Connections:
+3V3: CIN1.1, CIN2.1, CIN5.1, L3.1, U11.32 (VDDIOB), U11.37 (VDDIOB), U11.46 (VDDIO), U11.54 (VDDIO), U11.65 (VDDIO), U11.79 (VDDIO), U11.91 (VDDIO), U11.97 (VDDIO), U11.107 (VDDIO), U11.118 (VDDIO); also elsewhere on the board
ADC0 AIN0: U11.3 (PC00); also elsewhere on the board
ADC0 AIN1: U11.10 (PA03/AIN01); also elsewhere on the board
ADC0 AIN2: U11.19 (PB08/AIN02); also elsewhere on the board
ADC0 AIN3: U11.20 (PB09/AIN03); also elsewhere on the board
ADC0 AIN4: U11.21 (PA04/AIN04); also elsewhere on the board
ADC0 AIN5: U11.22 (PA05/AIN05); also elsewhere on the board
ADC0 AIN6: U11.23 (PA06/AIN06); also elsewhere on the board
ADC0 AIN7: U11.24 (PA07/AIN07); also elsewhere on the board
ADC0 AIN8: U11.33 (PA08/AIN08); also elsewhere on the board
ADC0 AIN9: U11.34 (PA09/AIN09); also elsewhere on the board
ADC0 AIN10: U11.35 (PA10/AIN10); also elsewhere on the board
ADC0 AIN11: U11.36 (PA11/AIN11); also elsewhere on the board
ADC0 AIN12: U11.125 (PB00/AIN12); also elsewhere on the board
ADC0 AIN13: U11.126 (PB01/AIN13); also elsewhere on the board
ADC0 AIN14: U11.127 (PB02/AIN14); also elsewhere on the board
ADC0 AIN15: U11.128 (PB03/AIN15); also elsewhere on the board
ADC1 AIN4: U11.7 (PC02); also elsewhere on the board
ADC1 AIN5: U11.8 (PC03); also elsewhere on the board
ADC1 AIN6: U11.11 (PB04); also elsewhere on the board
ADC1 AIN7: U11.12 (PB05); also elsewhere on the board
ADC1 AIN8: U11.17 (PB06); also elsewhere on the board
ADC1 AIN9: U11.18 (PB07); also elsewhere on the board
BURN CTRL: U11.105 (PB29); also elsewhere on the board
CAMERA MISO: U11.62 (PA14); also elsewhere on the board
CAMERA MOSI: U11.102 (PB26); also elsewhere on the board
CAMERA SCK: U11.103 (PB27); also elsewhere on the board
CAMERA ~CS: U11.58 (PC14); also elsewhere on the board
CAMERA/PVD/EPS SCL: U11.47 (PD08); also elsewhere on the board
CAMERA/PVD/EPS SDA: U11.48 (PD09); also elsewhere on the board
EPS A0: U11.87 (PB21); also elsewhere on the board
EPS A1: U11.98 (PB22); also elsewhere on the board
EPS A2: U11.99 (PB23); also elsewhere on the board
EPS IRQ: U11.104 (PB28); also elsewhere on the board
EPS ~RST: U11.86 (PB20); also elsewhere on the board
GND: CIN1.2, CIN2.2, CIN3.2, CIN4.2, CIN5.2, COUT1.2, COUT2.2, U11.5 (GND), U11.14 (GNDANA), U11.25 (GNDANA), U11.31 (GND), U11.38 (GND), U11.45 (GND), U11.53 (GND), U11.64 (GND), U11.78 (GND), U11.90 (GND), U11.96 (GND), U11.106 (GND), U11.116 (GNDIO); also elsewhere on the board
GYRO ~CS: U11.74 (PC20); also elsewhere on the board
GYRO ~DRDY: U11.76 (PC22); also elsewhere on the board
GYRO ~RST: U11.75 (PC21); also elsewhere on the board
HEATER 1: U11.77 (PC23); also elsewhere on the board
HEATER 2: U11.108 (PC24); also elsewhere on the board
LED ~ORANGE 1: U11.59 (PC15); also elsewhere on the board
LED ~ORANGE 2: U11.63 (PA15); also elsewhere on the board
LED ~RED: U11.69 (PA19); also elsewhere on the board
MAG ~CS: U11.73 (PC19); also elsewhere on the board
MAG ~DRDY: U11.52 (PC10); also elsewhere on the board
MAG/GYRO MISO: U11.43 (PB14); also elsewhere on the board
MAG/GYRO MOSI: U11.61 (PA13); also elsewhere on the board
MAG/GYRO SCK: U11.60 (PA12); also elsewhere on the board
MRAM 1 ~CS: U11.27 (PC04); also elsewhere on the board
MRAM 1 ~RESET: U11.28 (PC05); also elsewhere on the board
MRAM 1 ~WP: U11.41 (PB12); also elsewhere on the board
MRAM 2 ~CS: U11.29 (PC06); also elsewhere on the board
MRAM 2 ~RESET: U11.30 (PC07); also elsewhere on the board
MRAM 2 ~WP: U11.42 (PB13); also elsewhere on the board
MRAM 3 ~CS: U11.39 (PB10); also elsewhere on the board
MRAM 3 ~RESET: U11.40 (PB11); also elsewhere on the board
MRAM 3 ~WP: U11.44 (PB15); also elsewhere on the board
MRAM MISO: U11.72 (PC18); also elsewhere on the board
MRAM MOSI: U11.100 (PB24); also elsewhere on the board
MRAM SCK: U11.101 (PB25); also elsewhere on the board
MTQ_X_IN1: U11.88 (PA20); also elsewhere on the board
MTQ_X_IN2: U11.89 (PA21); also elsewhere on the board
MTQ_X_SLP: U11.121 (PB30); also elsewhere on the board
MTQ_Y_IN1: U11.92 (PA22); also elsewhere on the board
MTQ_Y_IN2: U11.93 (PA23); also elsewhere on the board
MTQ_Y_SLP: U11.122 (PB31); also elsewhere on the board
MTQ_Z_IN1: U11.80 (PD20); also elsewhere on the board
MTQ_Z_IN2: U11.81 (PD21); also elsewhere on the board
MTQ_Z_SLP: U11.111 (PC27); also elsewhere on the board
unnamed: COUT1.1, COUT2.1, L4.1, U11.115 (VDDCORE)
unnamed: L4.2, U11.117 (VSW)
OLED MOSI: U11.1 (PA00); also elsewhere on the board
OLED SCK: U11.2 (PA01); also elsewhere on the board
OLED ~CS: U11.55 (PC11); also elsewhere on the board
OLED ~D/C: U11.51 (PD12); also elsewhere on the board
OLED ~RST: U11.50 (PD11); also elsewhere on the board
PVD DAC: U11.9 (PA02/AIN00); also elsewhere on the board
SBAND EN: U11.109 (PC25); also elsewhere on the board
SBAND MISO: U11.84 (PB18); also elsewhere on the board
SBAND MOSI: U11.82 (PB16); also elsewhere on the board
SBAND SCK: U11.83 (PB17); also elsewhere on the board
SBAND SCL: U11.66 (PA16); also elsewhere on the board
SBAND SDA: U11.67 (PA17); also elsewhere on the board
SBAND ~CS: U11.85 (PB19); also elsewhere on the board
SBAND ~RST: U11.110 (PC26); also elsewhere on the board
SWCLK: U11.119 (PA30); also elsewhere on the board
SWD ~RESET: U11.114 (~RESET); also elsewhere on the board
SWDIO: U11.120 (PA31); also elsewhere on the board
UHF IRQ: U11.113 (PA27); also elsewhere on the board
UHF MISO: U11.49 (PD10); also elsewhere on the board
UHF MOSI: U11.56 (PC12); also elsewhere on the board
UHF SCK: U11.57 (PC13); also elsewhere on the board
UHF ~CS: U11.70 (PC16); also elsewhere on the board
UHF ~RESET: U11.71 (PC17); also elsewhere on the board
VDDANA: CIN3.1, CIN4.1, L3.2, U11.6 (VDDANA), U11.15 (VDDANA), U11.26 (VDDANA)

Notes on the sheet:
THERM 1
PHD 2
see https://github.com/BrownSpaceEngineering/PVDX-SAMD-PinConfig
PHD 8
THERM 2
(ADC1 AIN12 - UNUSED)
PHD 14
PHD 15
Power Circuit Place capacitors close to device
PHD 6
THERM 0
PHD 1
(UNALLOCATED)
PHD 17
PHD 7
(ADC1 AIN15 - UNUSED)
PHD 9
POWER
(ADC1 AIN14 - UNUSED)
PHD 12
PHD 11
PHD 3
PHD 5
PHD 0
PHD 13
(ADC1 AIN11 - UNUSED)
Milan Capoor 2026-09-29
(ADC1 AIN13 - UNUSED)
SAMD51 I/O
PHD 16
PHD 10
PEROVSKITE CTRL
PHD 4
THERM 3
PVDX COMPUTE BOARD - SAMD51

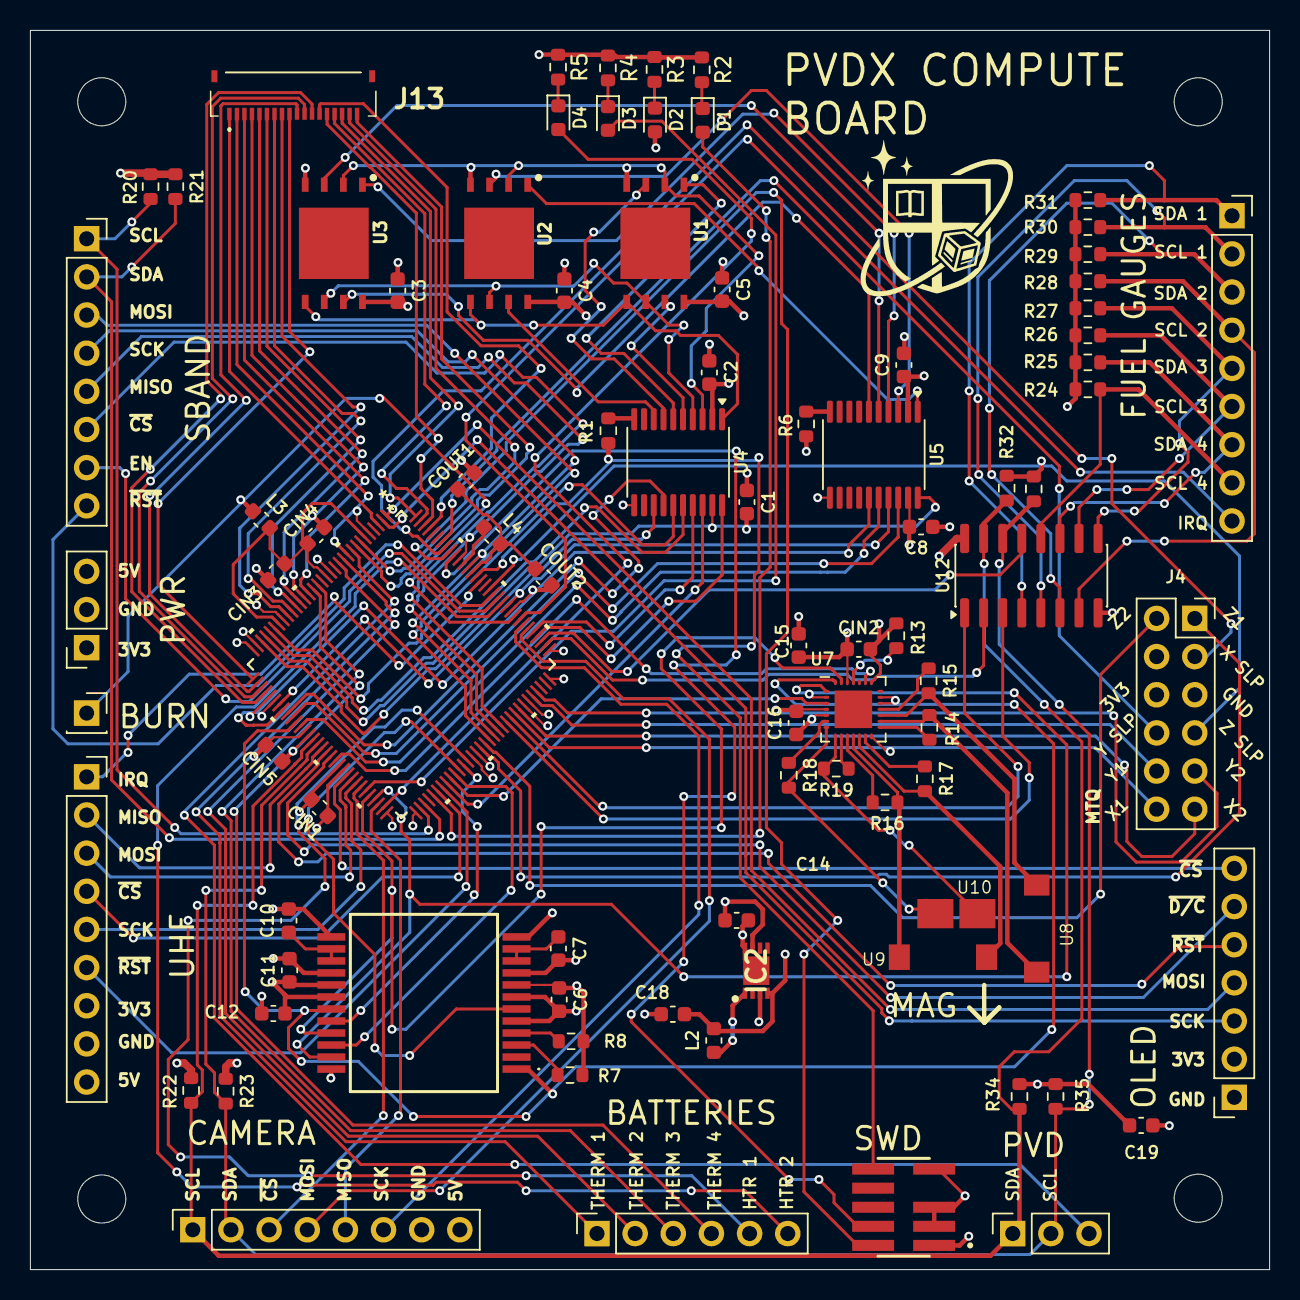
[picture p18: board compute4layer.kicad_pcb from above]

Board: 4 copper layers, 82.5 x 82.5 mm, 91 parts (0 on the bottom side), 142 nets.

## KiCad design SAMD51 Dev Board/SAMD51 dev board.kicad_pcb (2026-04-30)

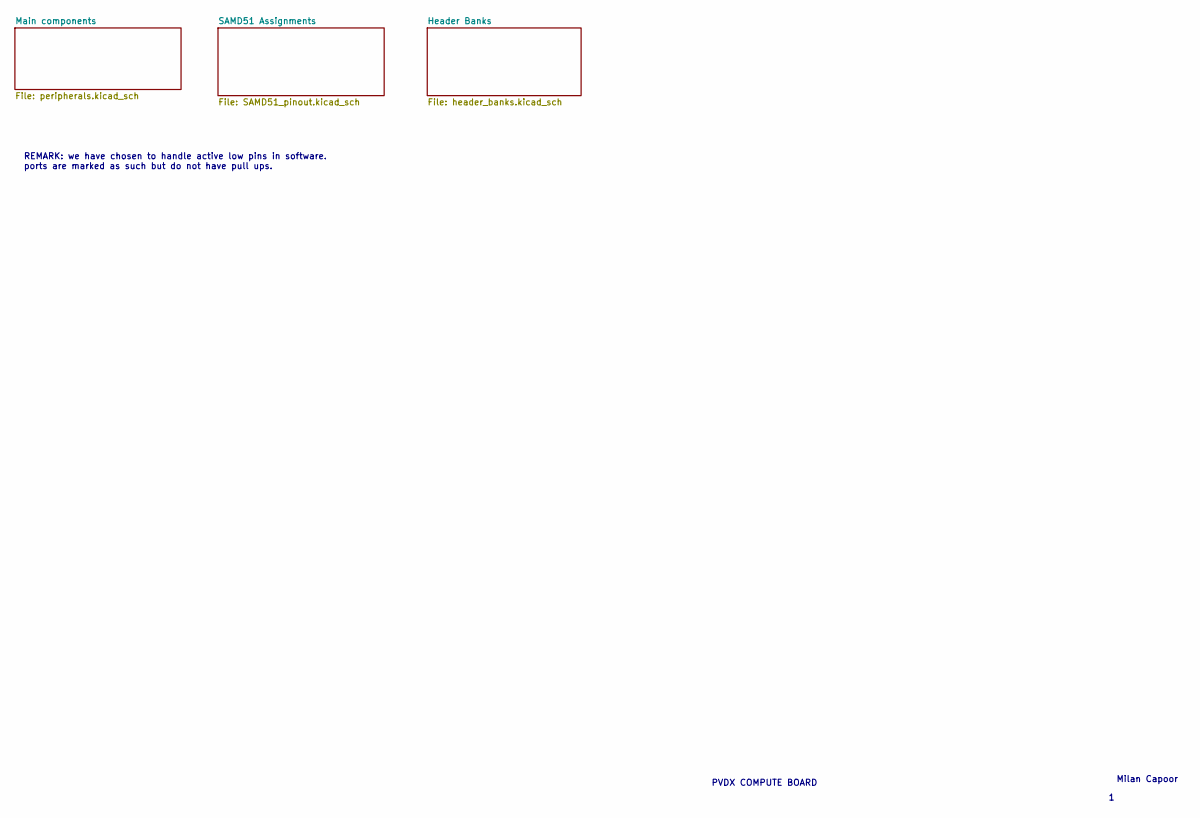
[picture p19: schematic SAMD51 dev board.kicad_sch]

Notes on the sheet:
REMARK: we have chosen to handle active low pins in software. ports are marked as such but do not have pull ups.
Milan Capoor
PVDX COMPUTE BOARD

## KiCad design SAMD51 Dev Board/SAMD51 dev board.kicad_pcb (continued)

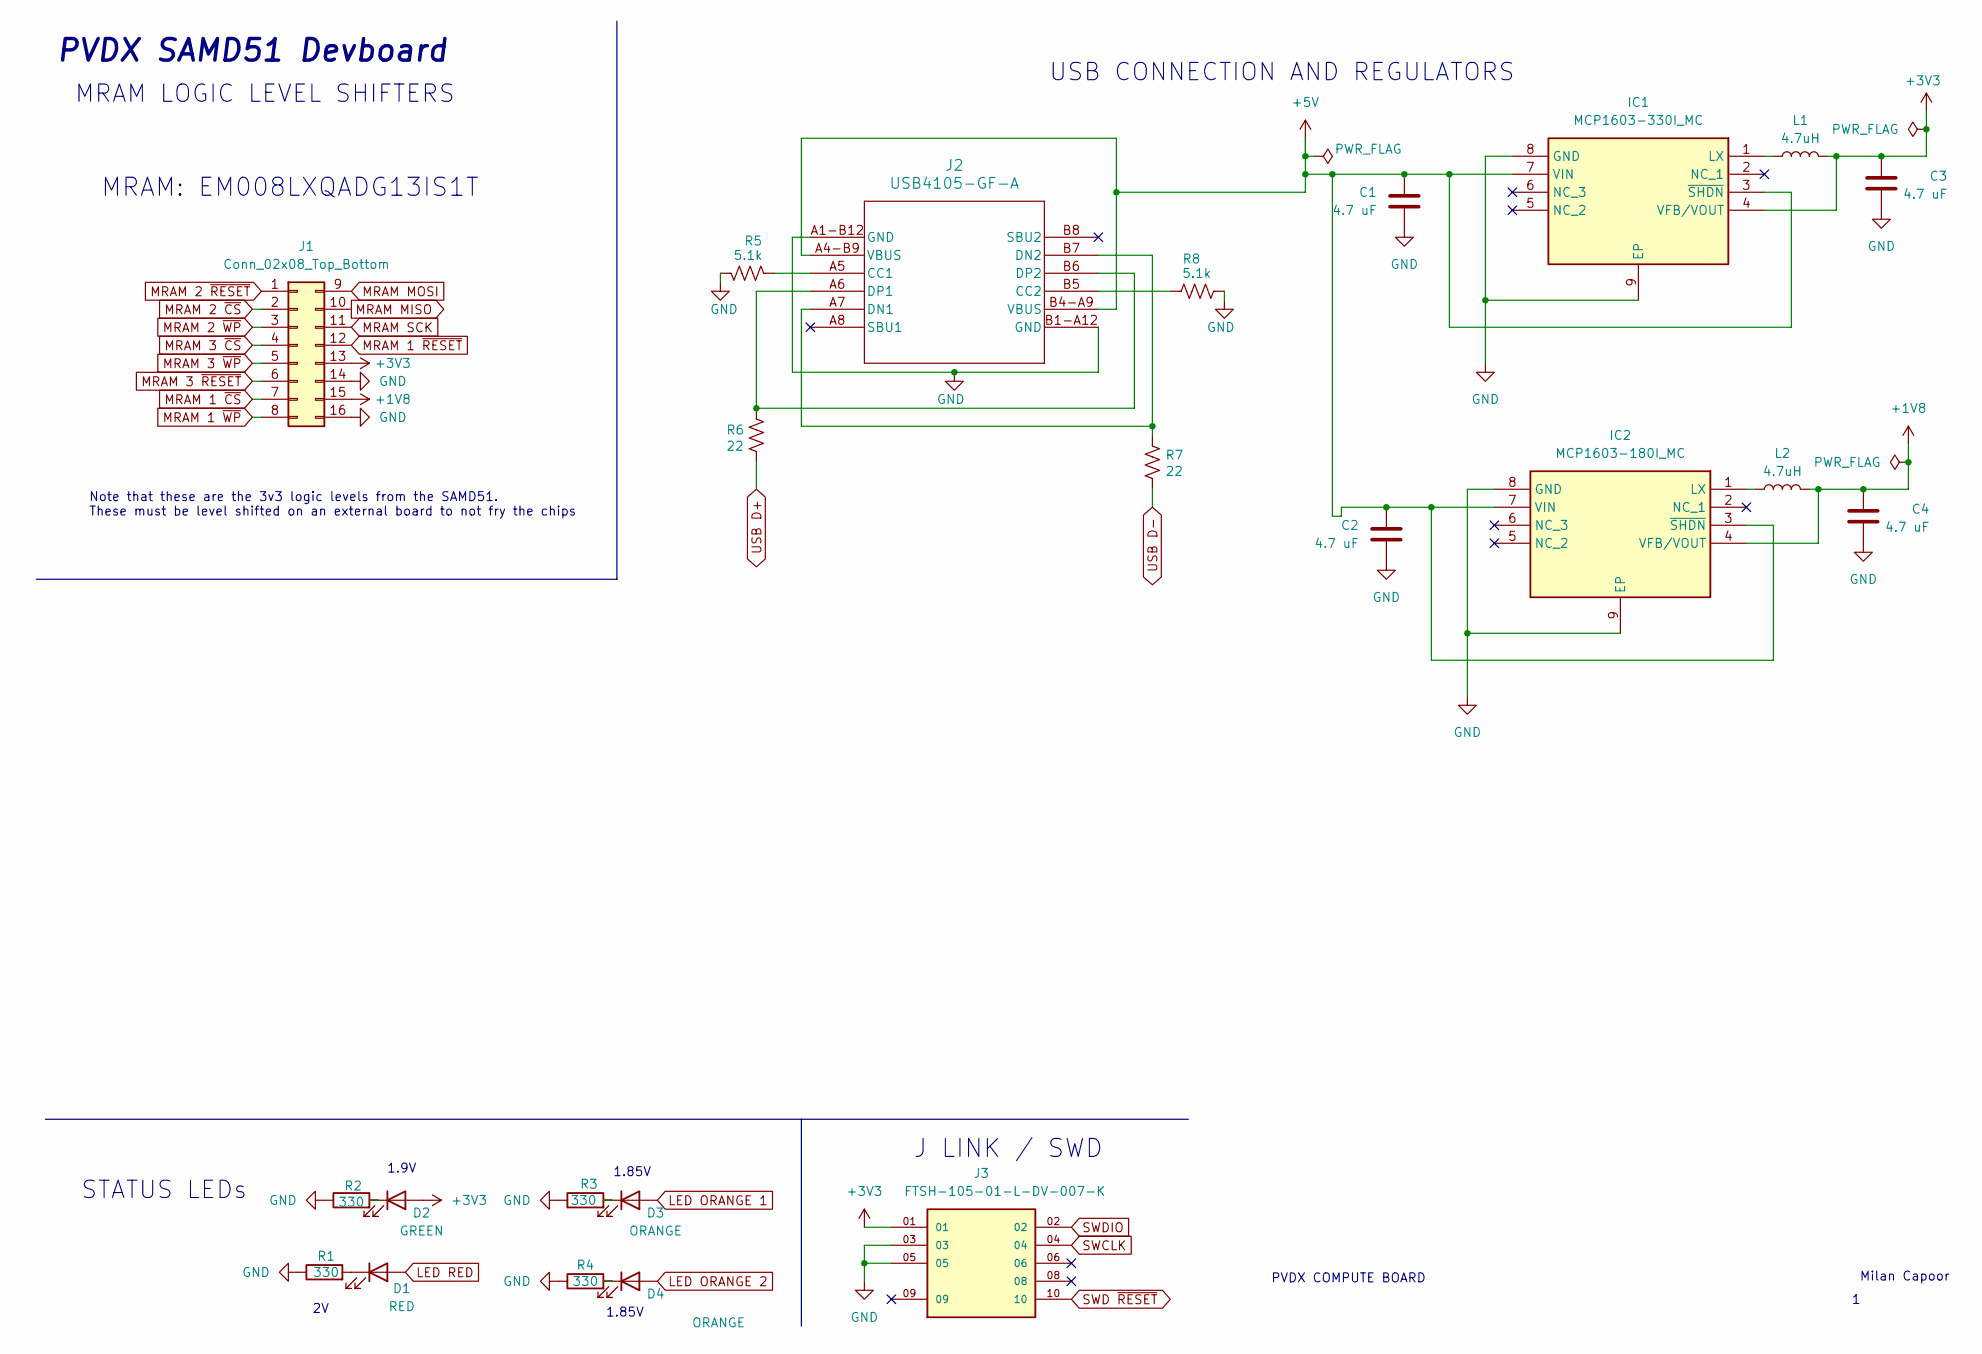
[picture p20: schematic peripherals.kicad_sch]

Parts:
C1, C2, C3, C4: 4.7 uF; C_0402_1005Metric
D1: RED; LED_0402_1005Metric
D2: GREEN; LED_0402_1005Metric
D3, D4: ORANGE; LED_0402_1005Metric
IC1: MCP1603-330I_MC; MPC1603-330; Mouser Part Number 579-MCP1603-330I/MC
IC2: MCP1603-180I_MC; MPC1603-180; Mouser Part Number 579-MCP1603-330I/MC
J1: Conn_02x08_Top_Bottom; PinSocket_2x08_P2.54mm_Vertical
J2: USB4105-GF-A; USB4105_GCT
J3: FTSH-105-01-L-DV-007-K; SAMTEC_FTSH-105-01-L-DV-007-K; PARTREV H
L1, L2: 4.7uH; L_0201_0603Metric
R1, R2, R3, R4: 330; R_0402_1005Metric
R5, R8: 5.1k; R_01005_0402Metric
R6, R7: 22; R_01005_0402Metric

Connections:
+1V8: C4.1, IC2.4 (VFB/VOUT), J1.15, L2.1; also elsewhere on the board
+3V3: C3.1, D2.2 (A), IC1.4 (VFB/VOUT), J1.13, J3.01, L1.1; also elsewhere on the board
+5V: C1.1, C2.1, IC1.3 (~SHDN), IC1.7 (VIN), IC2.3 (~SHDN), IC2.7 (VIN), J2.A4-B9 (VBUS), J2.B4-A9 (VBUS); also elsewhere on the board
GND: C1.2, C2.2, C3.2, C4.2, IC1.8 (GND), IC1.9 (EP), IC2.8 (GND), IC2.9 (EP), J1.14, J1.16, J2.A1-B12 (GND), J2.B1-A12 (GND), J3.03, J3.05, R1.1, R2.1, R3.1, R4.1, R5.2, R8.2; also elsewhere on the board
LED ORANGE 1: D3.2 (A); also elsewhere on the board
LED ORANGE 2: D4.2 (A); also elsewhere on the board
LED RED: D1.2 (A); also elsewhere on the board
MRAM 1 ~CS: J1.7; also elsewhere on the board
MRAM 1 ~RESET: J1.12; also elsewhere on the board
MRAM 1 ~WP: J1.8; also elsewhere on the board
MRAM 2 ~CS: J1.2; also elsewhere on the board
MRAM 2 ~RESET: J1.1; also elsewhere on the board
MRAM 2 ~WP: J1.3; also elsewhere on the board
MRAM 3 ~CS: J1.4; also elsewhere on the board
MRAM 3 ~RESET: J1.6; also elsewhere on the board
MRAM 3 ~WP: J1.5; also elsewhere on the board
MRAM MISO: J1.10; also elsewhere on the board
MRAM MOSI: J1.9; also elsewhere on the board
MRAM SCK: J1.11; also elsewhere on the board
unnamed: D1.1 (K), R1.2
unnamed: D2.1 (K), R2.2
unnamed: D3.1 (K), R3.2
unnamed: D4.1 (K), R4.2
unnamed: IC1.1 (LX), L1.2
unnamed: IC2.1 (LX), L2.2
unnamed: J2.A5 (CC1), R5.1
unnamed: J2.B5 (CC2), R8.1
unnamed: J2.A7 (DN1), J2.B7 (DN2), R7.1
unnamed: J2.A6 (DP1), J2.B6 (DP2), R6.1
SWCLK: J3.04; also elsewhere on the board
SWD ~RESET: J3.10; also elsewhere on the board
SWDIO: J3.02; also elsewhere on the board
USB D+: R6.2; also elsewhere on the board
USB D-: R7.2; also elsewhere on the board

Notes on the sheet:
USB CONNECTION AND REGULATORS
MRAM: EM008LXQADG13IS1T
STATUS LEDs
PVDX SAMD51 Devboard
Note that these are the 3v3 logic levels from the SAMD51. These must be level shifted on an external board to not fry the chips
MRAM LOGIC LEVEL SHIFTERS
1.85V
J LINK / SWD
1.9V
PVDX COMPUTE BOARD
Milan Capoor

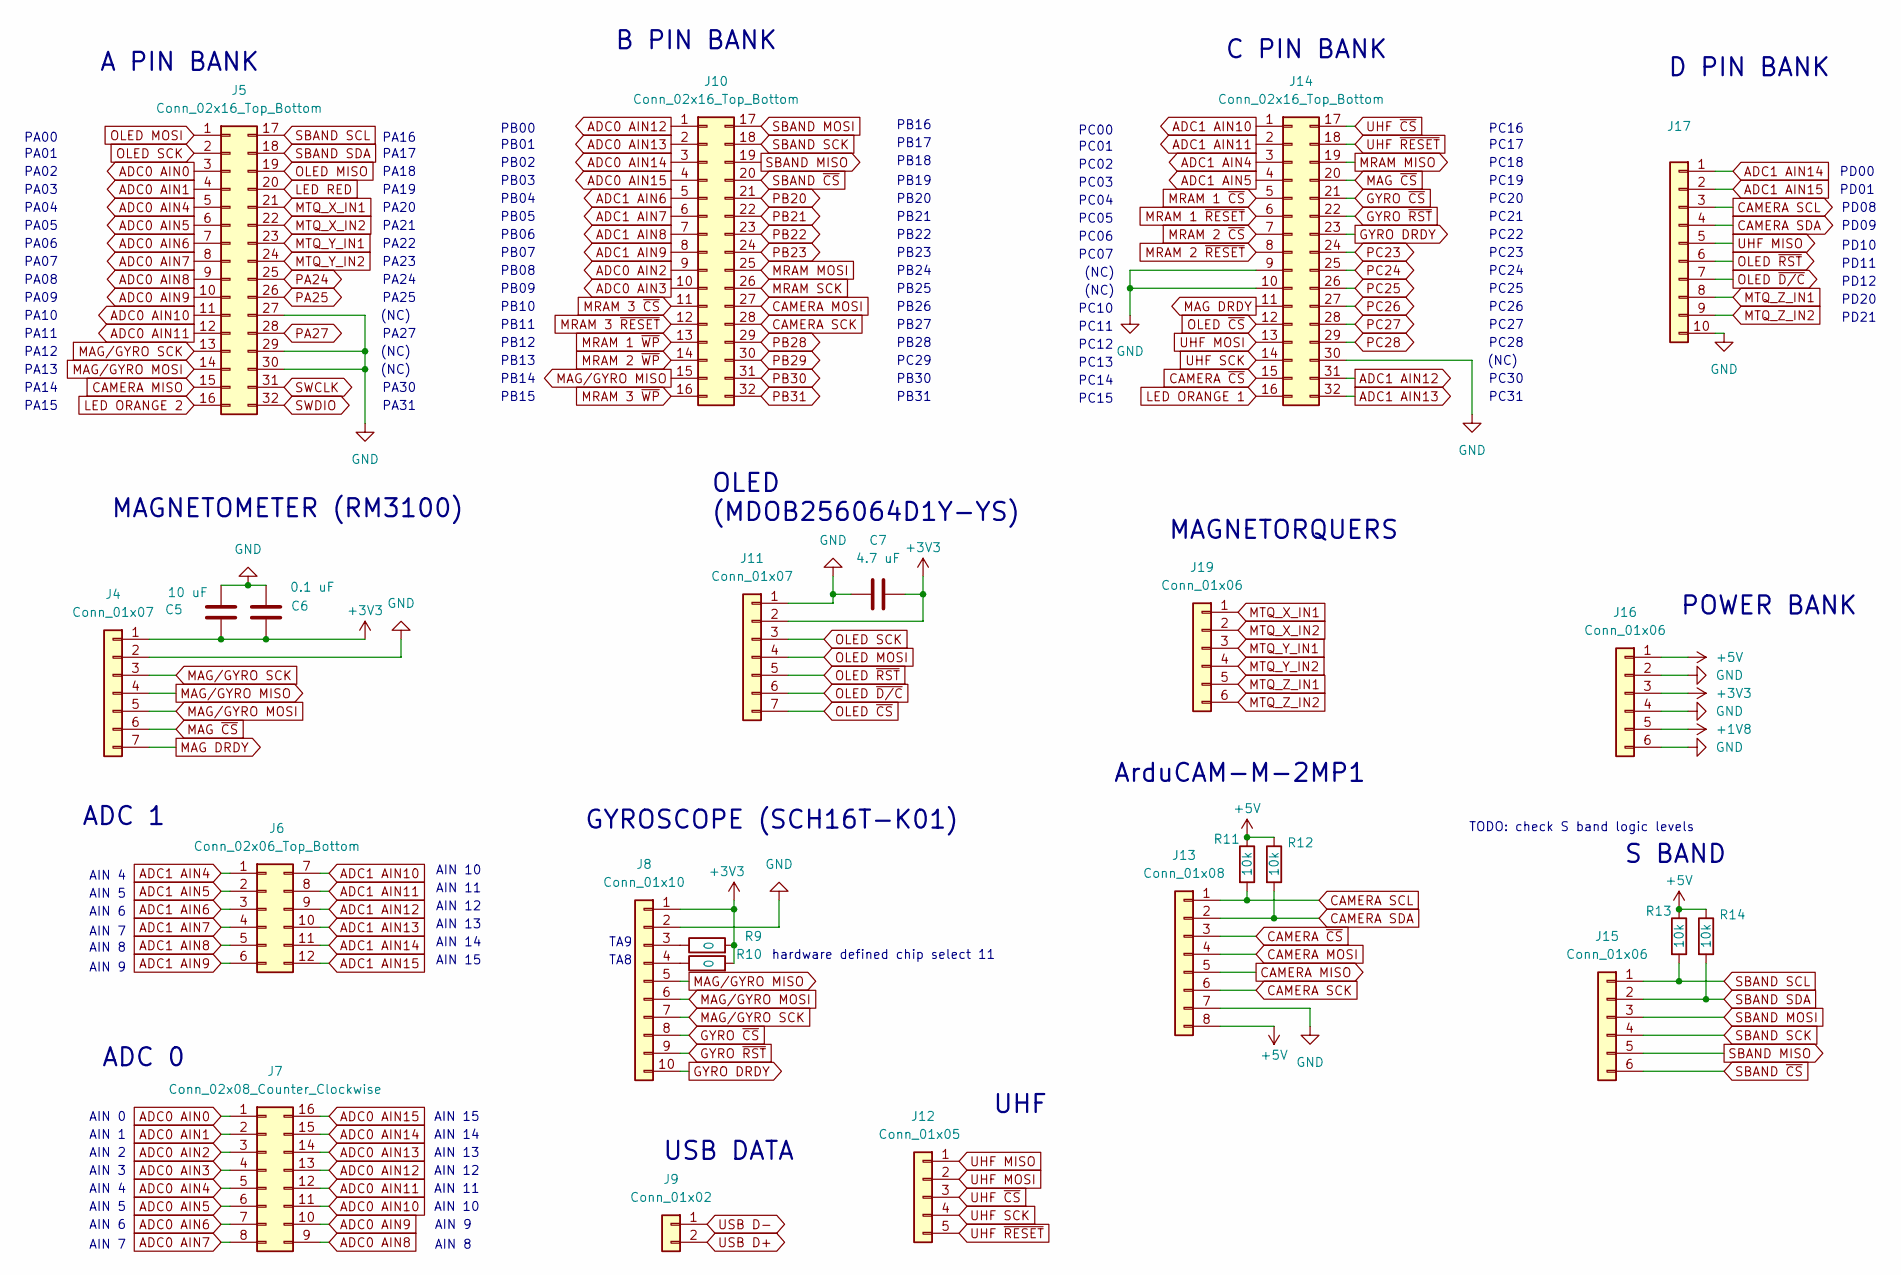
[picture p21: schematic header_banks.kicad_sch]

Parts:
C5: 10 uF; C_0402_1005Metric
C6: 0.1 uF; C_0402_1005Metric
C7: 4.7 uF; C_0402_1005Metric
J4, J11: Conn_01x07; PinSocket_1x07_P2.54mm_Vertical
J5, J10, J14: Conn_02x16_Top_Bottom; PinSocket_2x16_P2.54mm_Vertical
J6: Conn_02x06_Top_Bottom; PinSocket_2x06_P2.54mm_Vertical
J7: Conn_02x08_Counter_Clockwise; PinSocket_2x08_P2.54mm_Vertical
J8, J17: Conn_01x10; PinSocket_1x10_P2.54mm_Vertical
J9: Conn_01x02; PinSocket_1x02_P2.54mm_Vertical
J12: Conn_01x05; PinSocket_1x05_P2.54mm_Vertical
J13: Conn_01x08; PinSocket_1x08_P2.54mm_Vertical
J15, J16, J19: Conn_01x06; PinSocket_1x06_P2.54mm_Vertical
R9, R10: 0; R_0402_1005Metric
R11, R12, R13, R14: 10k; R_0402_1005Metric

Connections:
+1V8: J16.5; also elsewhere on the board
+3V3: C5.2, C6.2, C7.2, J4.1, J8.1, J11.2, J16.3, R9.2, R10.2; also elsewhere on the board
+5V: J13.8, J16.1, R11.1, R12.1, R13.1, R14.1; also elsewhere on the board
ADC0 AIN0: J5.3, J7.1; also elsewhere on the board
ADC0 AIN1: J5.4, J7.2; also elsewhere on the board
ADC0 AIN2: J7.3, J10.9; also elsewhere on the board
ADC0 AIN3: J7.4, J10.10; also elsewhere on the board
ADC0 AIN4: J5.5, J7.5; also elsewhere on the board
ADC0 AIN5: J5.6, J7.6; also elsewhere on the board
ADC0 AIN6: J5.7, J7.7; also elsewhere on the board
ADC0 AIN7: J5.8, J7.8; also elsewhere on the board
ADC0 AIN8: J5.9, J7.9; also elsewhere on the board
ADC0 AIN9: J5.10, J7.10; also elsewhere on the board
ADC0 AIN10: J5.11, J7.11; also elsewhere on the board
ADC0 AIN11: J5.12, J7.12; also elsewhere on the board
ADC0 AIN12: J7.13, J10.1; also elsewhere on the board
ADC0 AIN13: J7.14, J10.2; also elsewhere on the board
ADC0 AIN14: J7.15, J10.3; also elsewhere on the board
ADC0 AIN15: J7.16, J10.4; also elsewhere on the board
ADC1 AIN4: J6.1, J14.3; also elsewhere on the board
ADC1 AIN5: J6.2, J14.4; also elsewhere on the board
ADC1 AIN6: J6.3, J10.5; also elsewhere on the board
ADC1 AIN7: J6.4, J10.6; also elsewhere on the board
ADC1 AIN8: J6.5, J10.7; also elsewhere on the board
ADC1 AIN9: J6.6, J10.8; also elsewhere on the board
ADC1 AIN10: J6.7, J14.1; also elsewhere on the board
ADC1 AIN11: J6.8, J14.2; also elsewhere on the board
ADC1 AIN12: J6.9, J14.31; also elsewhere on the board
ADC1 AIN13: J6.10, J14.32; also elsewhere on the board
ADC1 AIN14: J6.11, J17.1; also elsewhere on the board
ADC1 AIN15: J6.12, J17.2; also elsewhere on the board
CAMERA MISO: J5.15, J13.5; also elsewhere on the board
CAMERA MOSI: J10.27, J13.4; also elsewhere on the board
CAMERA SCK: J10.28, J13.6; also elsewhere on the board
CAMERA SCL: J13.1, J17.3, R11.2; also elsewhere on the board
CAMERA SDA: J13.2, J17.4, R12.2; also elsewhere on the board
CAMERA ~CS: J13.3, J14.15; also elsewhere on the board
GND: C5.1, C6.1, C7.1, J4.2, J5.27, J5.29, J5.30, J8.2, J11.1, J13.7, J14.9, J14.10, J14.30, J16.2, J16.4, J16.6, J17.10; also elsewhere on the board
GYRO DRDY: J8.10, J14.23; also elsewhere on the board
GYRO ~CS: J8.8, J14.21; also elsewhere on the board
GYRO ~RST: J8.9, J14.22; also elsewhere on the board
LED ORANGE 1: J14.16; also elsewhere on the board
LED ORANGE 2: J5.16; also elsewhere on the board
LED RED: J5.20; also elsewhere on the board
MAG DRDY: J4.7, J14.11; also elsewhere on the board
MAG ~CS: J4.6, J14.20; also elsewhere on the board
MAG/GYRO MISO: J4.4, J8.5, J10.15; also elsewhere on the board
MAG/GYRO MOSI: J4.5, J5.14, J8.6; also elsewhere on the board
MAG/GYRO SCK: J4.3, J5.13, J8.7; also elsewhere on the board
MRAM 1 ~CS: J14.5; also elsewhere on the board
MRAM 1 ~RESET: J14.6; also elsewhere on the board
MRAM 1 ~WP: J10.13; also elsewhere on the board
MRAM 2 ~CS: J14.7; also elsewhere on the board
MRAM 2 ~RESET: J14.8; also elsewhere on the board
MRAM 2 ~WP: J10.14; also elsewhere on the board
MRAM 3 ~CS: J10.11; also elsewhere on the board
MRAM 3 ~RESET: J10.12; also elsewhere on the board
MRAM 3 ~WP: J10.16; also elsewhere on the board
MRAM MISO: J14.19; also elsewhere on the board
MRAM MOSI: J10.25; also elsewhere on the board
MRAM SCK: J10.26; also elsewhere on the board
MTQ_X_IN1: J5.21, J19.1; also elsewhere on the board
MTQ_X_IN2: J5.22, J19.2; also elsewhere on the board
MTQ_Y_IN1: J5.23, J19.3; also elsewhere on the board
MTQ_Y_IN2: J5.24, J19.4; also elsewhere on the board
MTQ_Z_IN1: J17.8, J19.5; also elsewhere on the board
MTQ_Z_IN2: J17.9, J19.6; also elsewhere on the board
unnamed: J8.3, R9.1
unnamed: J8.4, R10.1
OLED MISO: J5.19; also elsewhere on the board
OLED MOSI: J5.1, J11.4; also elsewhere on the board
OLED SCK: J5.2, J11.3; also elsewhere on the board
OLED ~CS: J11.7, J14.12; also elsewhere on the board
OLED ~D/C: J11.6, J17.7; also elsewhere on the board
OLED ~RST: J11.5, J17.6; also elsewhere on the board
PA24: J5.25; also elsewhere on the board
PA25: J5.26; also elsewhere on the board
PA27: J5.28; also elsewhere on the board
PB20: J10.21; also elsewhere on the board
PB21: J10.22; also elsewhere on the board
PB22: J10.23; also elsewhere on the board
PB23: J10.24; also elsewhere on the board
PB28: J10.29; also elsewhere on the board
PB29: J10.30; also elsewhere on the board
PB30: J10.31; also elsewhere on the board
PB31: J10.32; also elsewhere on the board
PC23: J14.24; also elsewhere on the board
PC24: J14.25; also elsewhere on the board
PC25: J14.26; also elsewhere on the board
PC26: J14.27; also elsewhere on the board
PC27: J14.28; also elsewhere on the board
PC28: J14.29; also elsewhere on the board
SBAND MISO: J10.19, J15.5; also elsewhere on the board
SBAND MOSI: J10.17, J15.3; also elsewhere on the board
SBAND SCK: J10.18, J15.4; also elsewhere on the board
SBAND SCL: J5.17, J15.1, R13.2; also elsewhere on the board
SBAND SDA: J5.18, J15.2, R14.2; also elsewhere on the board
SBAND ~CS: J10.20, J15.6; also elsewhere on the board
SWCLK: J5.31; also elsewhere on the board
SWDIO: J5.32; also elsewhere on the board
UHF MISO: J12.1, J17.5; also elsewhere on the board
UHF MOSI: J12.2, J14.13; also elsewhere on the board
UHF SCK: J12.4, J14.14; also elsewhere on the board
UHF ~CS: J12.3, J14.17; also elsewhere on the board
UHF ~RESET: J12.5, J14.18; also elsewhere on the board
USB D+: J9.2; also elsewhere on the board
USB D-: J9.1; also elsewhere on the board

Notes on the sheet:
AIN 12
PA24
PB00
PC07
PC29
PC18
PC05
AIN 13
AIN 11
PC16
PB11
PC26
PA15
TA9
PC03
PD20
(NC)
PA16
PB10
PB03
C PIN BANK
PA09
PA23
OLED (MDOB256064D1Y-YS)
PA14
PD00
PB20
PD21
AIN 4
ADC 0
PA21
PC22
PB08
A PIN BANK
PB24
AIN 8
PC23
PA31
PA25
AIN 14

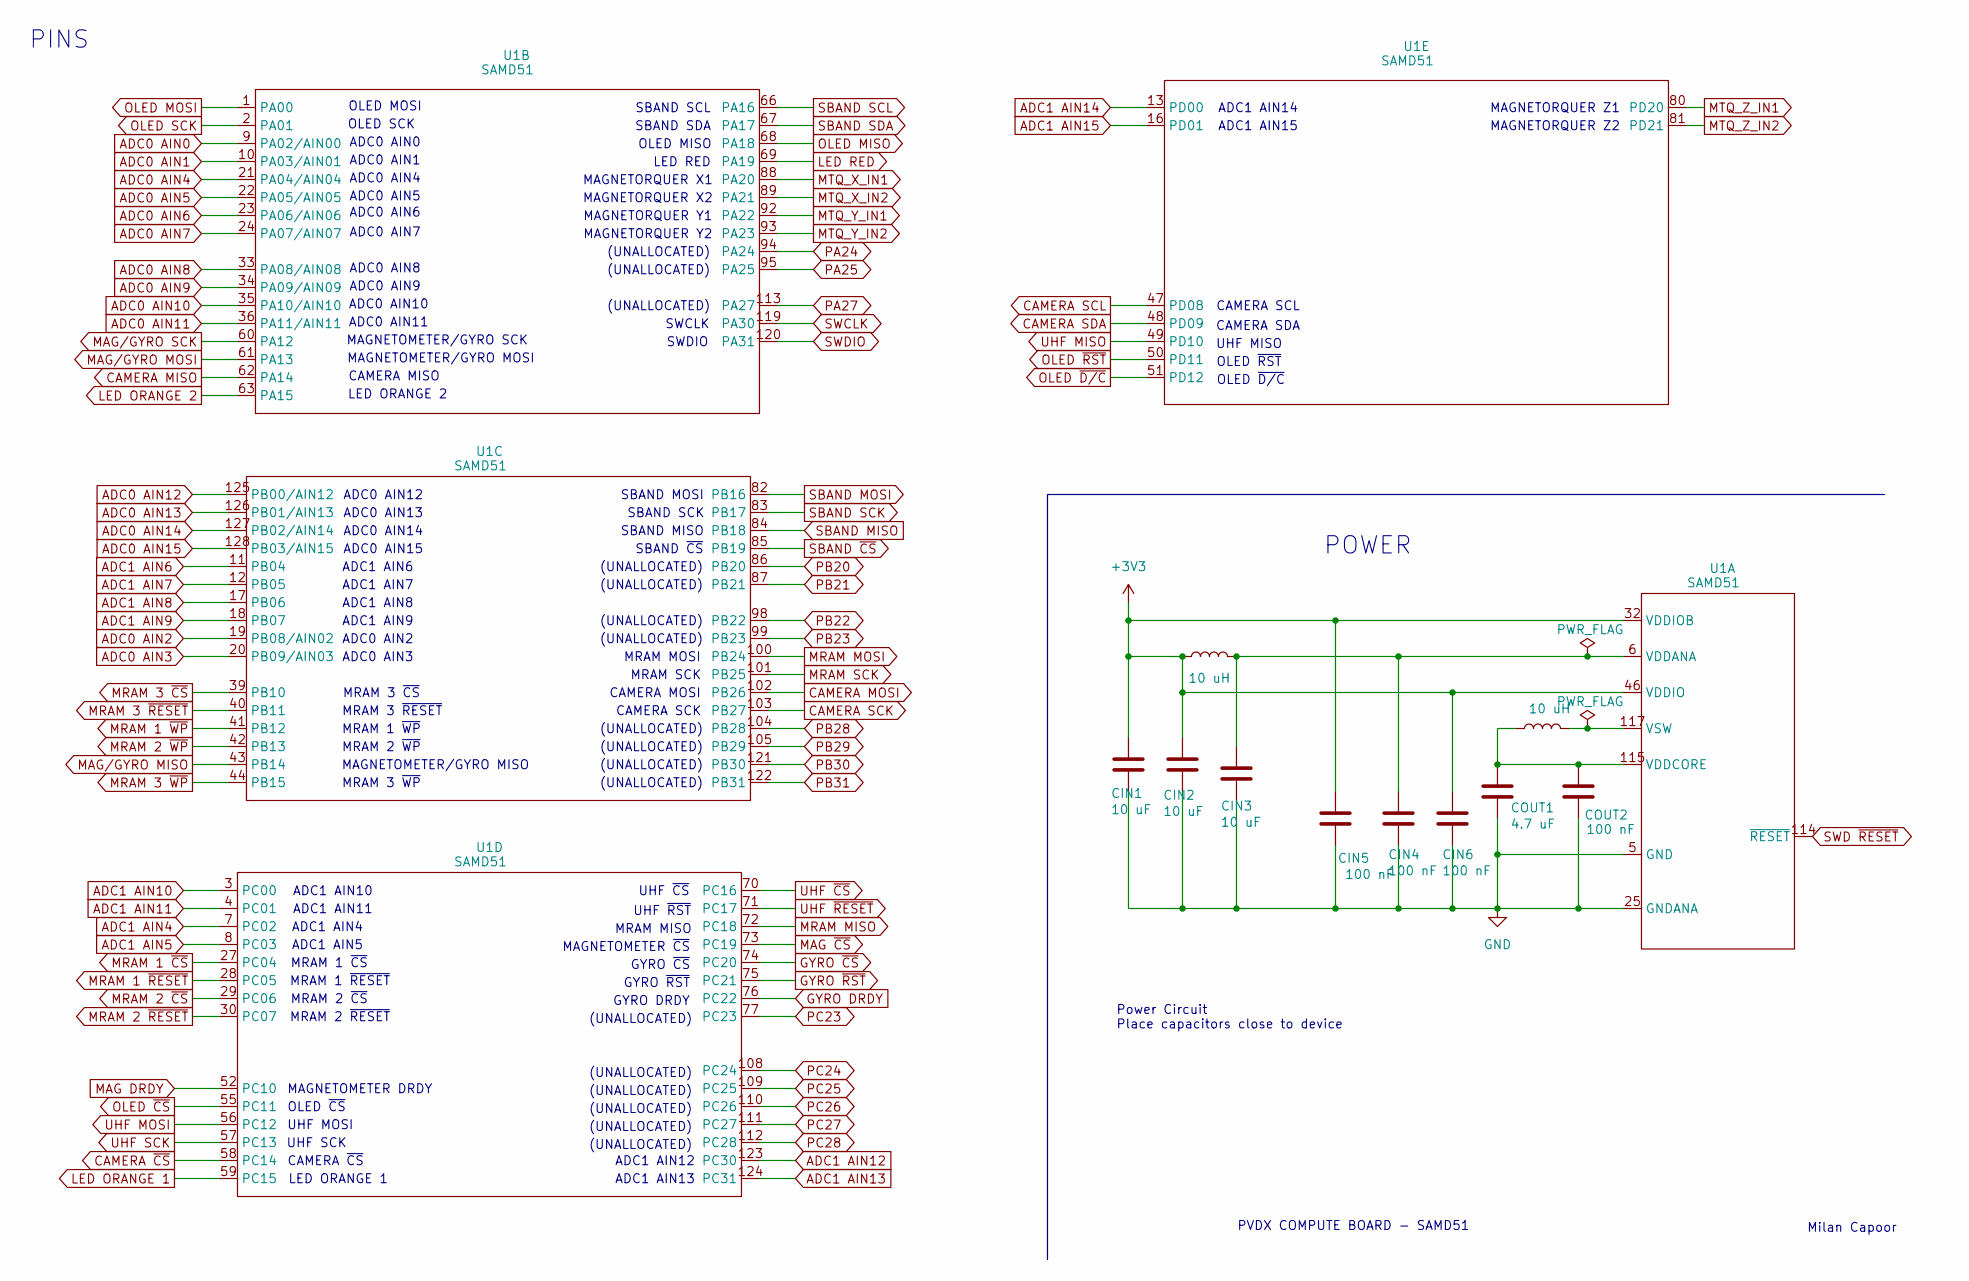
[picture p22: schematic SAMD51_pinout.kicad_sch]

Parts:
CIN1, CIN2, CIN3: 10 uF; C_0402_1005Metric
CIN4, CIN5, CIN6: 100 nF; C_0402_1005Metric
COUT1: 4.7 uF; C_0402_1005Metric
COUT2: 100 nF; C_0402_1005Metric
L3, L4: 10 uH; L_0402_1005Metric
U1: SAMD51; TQFP128_14X14MC_MCH-L

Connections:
+3V3: CIN1.1, CIN2.1, CIN5.1, CIN6.1, L3.1, U1.32 (VDDIOB), U1.37 (VDDIOB), U1.46 (VDDIO), U1.54 (VDDIO), U1.65 (VDDIO), U1.79 (VDDIO), U1.91 (VDDIO), U1.97 (VDDIO), U1.107 (VDDIO), U1.118 (VDDIO); also elsewhere on the board
ADC0 AIN0: U1.9 (PA02/AIN00); also elsewhere on the board
ADC0 AIN1: U1.10 (PA03/AIN01); also elsewhere on the board
ADC0 AIN2: U1.19 (PB08/AIN02); also elsewhere on the board
ADC0 AIN3: U1.20 (PB09/AIN03); also elsewhere on the board
ADC0 AIN4: U1.21 (PA04/AIN04); also elsewhere on the board
ADC0 AIN5: U1.22 (PA05/AIN05); also elsewhere on the board
ADC0 AIN6: U1.23 (PA06/AIN06); also elsewhere on the board
ADC0 AIN7: U1.24 (PA07/AIN07); also elsewhere on the board
ADC0 AIN8: U1.33 (PA08/AIN08); also elsewhere on the board
ADC0 AIN9: U1.34 (PA09/AIN09); also elsewhere on the board
ADC0 AIN10: U1.35 (PA10/AIN10); also elsewhere on the board
ADC0 AIN11: U1.36 (PA11/AIN11); also elsewhere on the board
ADC0 AIN12: U1.125 (PB00/AIN12); also elsewhere on the board
ADC0 AIN13: U1.126 (PB01/AIN13); also elsewhere on the board
ADC0 AIN14: U1.127 (PB02/AIN14); also elsewhere on the board
ADC0 AIN15: U1.128 (PB03/AIN15); also elsewhere on the board
ADC1 AIN4: U1.7 (PC02); also elsewhere on the board
ADC1 AIN5: U1.8 (PC03); also elsewhere on the board
ADC1 AIN6: U1.11 (PB04); also elsewhere on the board
ADC1 AIN7: U1.12 (PB05); also elsewhere on the board
ADC1 AIN8: U1.17 (PB06); also elsewhere on the board
ADC1 AIN9: U1.18 (PB07); also elsewhere on the board
ADC1 AIN10: U1.3 (PC00); also elsewhere on the board
ADC1 AIN11: U1.4 (PC01); also elsewhere on the board
ADC1 AIN12: U1.123 (PC30); also elsewhere on the board
ADC1 AIN13: U1.124 (PC31); also elsewhere on the board
ADC1 AIN14: U1.13 (PD00); also elsewhere on the board
ADC1 AIN15: U1.16 (PD01); also elsewhere on the board
CAMERA MISO: U1.62 (PA14); also elsewhere on the board
CAMERA MOSI: U1.102 (PB26); also elsewhere on the board
CAMERA SCK: U1.103 (PB27); also elsewhere on the board
CAMERA SCL: U1.47 (PD08); also elsewhere on the board
CAMERA SDA: U1.48 (PD09); also elsewhere on the board
CAMERA ~CS: U1.58 (PC14); also elsewhere on the board
GND: CIN1.2, CIN2.2, CIN3.2, CIN4.2, CIN5.2, CIN6.2, COUT1.2, COUT2.2, U1.5 (GND), U1.14 (GNDANA), U1.25 (GNDANA), U1.31 (GND), U1.38 (GND), U1.45 (GND), U1.53 (GND), U1.64 (GND), U1.78 (GND), U1.90 (GND), U1.96 (GND), U1.106 (GND); also elsewhere on the board
GYRO DRDY: U1.76 (PC22); also elsewhere on the board
GYRO ~CS: U1.74 (PC20); also elsewhere on the board
GYRO ~RST: U1.75 (PC21); also elsewhere on the board
LED ORANGE 1: U1.59 (PC15); also elsewhere on the board
LED ORANGE 2: U1.63 (PA15); also elsewhere on the board
LED RED: U1.69 (PA19); also elsewhere on the board
MAG DRDY: U1.52 (PC10); also elsewhere on the board
MAG ~CS: U1.73 (PC19); also elsewhere on the board
MAG/GYRO MISO: U1.43 (PB14); also elsewhere on the board
MAG/GYRO MOSI: U1.61 (PA13); also elsewhere on the board
MAG/GYRO SCK: U1.60 (PA12); also elsewhere on the board
MRAM 1 ~CS: U1.27 (PC04); also elsewhere on the board
MRAM 1 ~RESET: U1.28 (PC05); also elsewhere on the board
MRAM 1 ~WP: U1.41 (PB12); also elsewhere on the board
MRAM 2 ~CS: U1.29 (PC06); also elsewhere on the board
MRAM 2 ~RESET: U1.30 (PC07); also elsewhere on the board
MRAM 2 ~WP: U1.42 (PB13); also elsewhere on the board
MRAM 3 ~CS: U1.39 (PB10); also elsewhere on the board
MRAM 3 ~RESET: U1.40 (PB11); also elsewhere on the board
MRAM 3 ~WP: U1.44 (PB15); also elsewhere on the board
MRAM MISO: U1.72 (PC18); also elsewhere on the board
MRAM MOSI: U1.100 (PB24); also elsewhere on the board
MRAM SCK: U1.101 (PB25); also elsewhere on the board
MTQ_X_IN1: U1.88 (PA20); also elsewhere on the board
MTQ_X_IN2: U1.89 (PA21); also elsewhere on the board
MTQ_Y_IN1: U1.92 (PA22); also elsewhere on the board
MTQ_Y_IN2: U1.93 (PA23); also elsewhere on the board
MTQ_Z_IN1: U1.80 (PD20); also elsewhere on the board
MTQ_Z_IN2: U1.81 (PD21); also elsewhere on the board
unnamed: CIN3.1, CIN4.1, L3.2, U1.6 (VDDANA), U1.15 (VDDANA), U1.26 (VDDANA)
unnamed: COUT1.1, COUT2.1, L4.1, U1.115 (VDDCORE)
unnamed: L4.2, U1.117 (VSW)
OLED MISO: U1.68 (PA18); also elsewhere on the board
OLED MOSI: U1.1 (PA00); also elsewhere on the board
OLED SCK: U1.2 (PA01); also elsewhere on the board
OLED ~CS: U1.55 (PC11); also elsewhere on the board
OLED ~D/C: U1.51 (PD12); also elsewhere on the board
OLED ~RST: U1.50 (PD11); also elsewhere on the board
PA24: U1.94 (PA24); also elsewhere on the board
PA25: U1.95 (PA25); also elsewhere on the board
PA27: U1.113 (PA27); also elsewhere on the board
PB20: U1.86 (PB20); also elsewhere on the board
PB21: U1.87 (PB21); also elsewhere on the board
PB22: U1.98 (PB22); also elsewhere on the board
PB23: U1.99 (PB23); also elsewhere on the board
PB28: U1.104 (PB28); also elsewhere on the board
PB29: U1.105 (PB29); also elsewhere on the board
PB30: U1.121 (PB30); also elsewhere on the board
PB31: U1.122 (PB31); also elsewhere on the board
PC23: U1.77 (PC23); also elsewhere on the board
PC24: U1.108 (PC24); also elsewhere on the board
PC25: U1.109 (PC25); also elsewhere on the board
PC26: U1.110 (PC26); also elsewhere on the board
PC27: U1.111 (PC27); also elsewhere on the board
PC28: U1.112 (PC28); also elsewhere on the board
SBAND MISO: U1.84 (PB18); also elsewhere on the board
SBAND MOSI: U1.82 (PB16); also elsewhere on the board
SBAND SCK: U1.83 (PB17); also elsewhere on the board
SBAND SCL: U1.66 (PA16); also elsewhere on the board
SBAND SDA: U1.67 (PA17); also elsewhere on the board
SBAND ~CS: U1.85 (PB19); also elsewhere on the board
SWCLK: U1.119 (PA30); also elsewhere on the board
SWD ~RESET: U1.114 (~RESET); also elsewhere on the board
SWDIO: U1.120 (PA31); also elsewhere on the board
UHF MISO: U1.49 (PD10); also elsewhere on the board
UHF MOSI: U1.56 (PC12); also elsewhere on the board
UHF SCK: U1.57 (PC13); also elsewhere on the board
UHF ~CS: U1.70 (PC16); also elsewhere on the board
UHF ~RESET: U1.71 (PC17); also elsewhere on the board

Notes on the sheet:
(UNALLOCATED)
ADC0 AIN3
MRAM MISO
ADC0 AIN9
GYRO ~{CS}
CAMERA ~{CS}
PINS
LED ORANGE 2
SWCLK
CAMERA SCL
OLED ~{D/C}
ADC0 AIN12
OLED MOSI
MAGNETORQUER X2
ADC0 AIN6
UHF MISO
MAGNETOMETER/GYRO MOSI
SWDIO
ADC1 AIN12
MRAM 1 ~{CS}
Power Circuit Place capacitors close to device
ADC1 AIN9
MAGNETOMETER ~{CS}
ADC0 AIN4
OLED ~{CS}
ADC1 AIN7
LED ORANGE 1
ADC0 AIN15
ADC1 AIN8
CAMERA SCK
CAMERA MOSI
UHF SCK
SBAND SCL
MRAM 3 ~{CS}
POWER
LED RED
OLED SCK
ADC1 AIN4
ADC1 AIN13
ADC0 AIN5

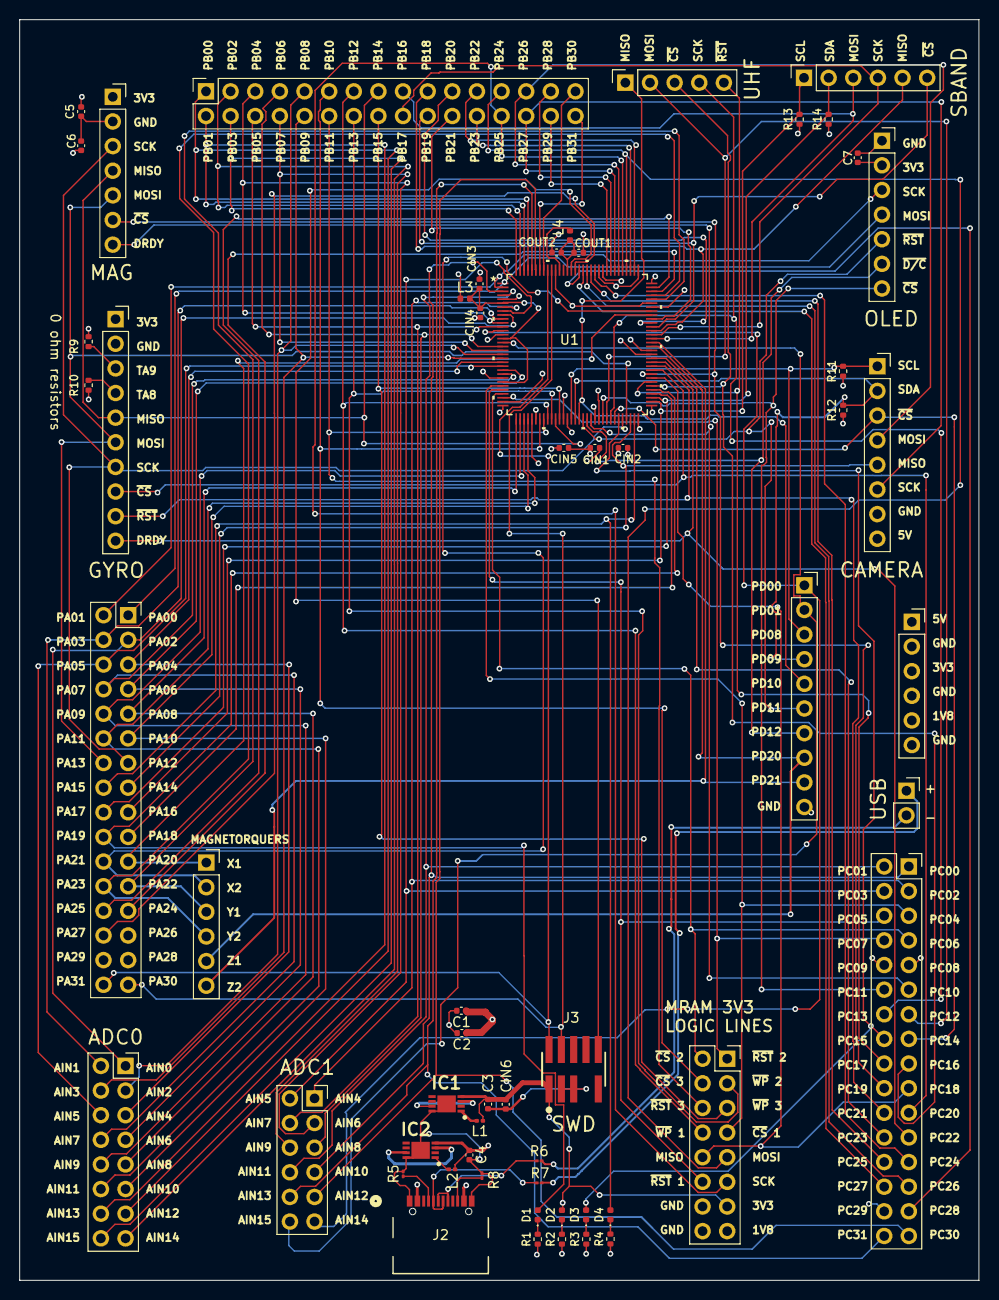
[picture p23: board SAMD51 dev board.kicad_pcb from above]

Board: 4 copper layers, 98.9 x 130.0 mm, 58 parts (0 on the bottom side), 121 nets.

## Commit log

2025-11-14 update draft to 11/13 version
    [EDI2CAP.CFG, PI3B3251QE.SchLib, PI3B3251QE.stp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]
2025-12-05 Redid layout to separate analog/digital traces
    [PVDX Compute Board.kicad_pcb]
2026-03-06 updated pins to match new spec and exposed all pins
    [PVDX Compute Board.kicad_pcb, PVDX Compute Board.kicad_sch, SAMD51_pinout.kicad_sch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]
2026-04-07 reorganized repo and added samd breakout
    [EDI2CAP.CFG, FTSH-105-01-L-DV-007-K.step, FTSH-105-01-L-DV-007-K.stp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]
2026-04-14 routed samd51 breakout
    [SAMD51 dev board.kicad_pcb, SAMD51_pinout.kicad_sch, header_banks.kicad_sch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]
2026-04-30 Fix USBC and regulators on samd breakout board, changes need to be added to compute board.
    [FTSH-105-01-L-DV-007-K.step, FTSH-105-01-L-DV-007-K.stp, MagIC QFN 4X4.STEP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]
2026-05-14 Update LED resistor values
    [SAMD51 dev board.csv, peripherals.kicad_sch]

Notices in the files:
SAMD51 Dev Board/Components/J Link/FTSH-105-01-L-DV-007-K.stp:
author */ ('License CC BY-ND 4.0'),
